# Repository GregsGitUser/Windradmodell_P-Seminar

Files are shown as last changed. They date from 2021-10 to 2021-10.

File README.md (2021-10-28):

# Windradmodell_P-Seminar
CAD-Dateien der von mir erstellten Teile und der Code, der auf dem Arduino Nano läuft. Außerdem noch die source-Dateien für die Platine, die ich für dieses Projekt gemacht habe

Im Rahmen des P-Seminars Physik am ITG 2020-22 mit dem Thema Klimawandel

Wir wollten ein Windradmodell bauen und an diesem verschiedene Messungen durchführen. Als Zusatzfunktion sollte es noch der Windrichtung folgen,
was durch einen Schrittmotor (NEMA 17-03 mit 20Nm und 0,2A) in der Basis des Windrads und einen Zweipunktregler möglich wurde. Zur Ansteuerung wird ein A4988 Treiber verwendet.
Der Microcontroller ist ein Arduino Nano, der als Interface einen Drehenkoder (KY-040) und Kippschalter hat. So kann auch die Regelungsgeschwindigkeit für den Zweipunktregler
eingestellt werden. Informationen können auf einem 16x2 LCD-Bildschirm abgelesen werden, der über I2c (mit I2c Bus) mit dem Microcontroller kommuniziert. 
Ein generisches Gleichstromnetzteil dient als Stromversorgung.

Oben in der Gondel des Windrads ist ein kleiner Generator, dessen Ausgangsleistung an einem Lastwiderstand (>2 Ohm) abfällt.
Die Spannung, welche über dem Widerstand abfällt, kann direkt analog mit dem internen 10-Bit ADC eingelesen werden, weil sie 5V (die Logikspannung des Nanos) nie überschreitet.
Aus diesen Werten kann die insgesamte elektrische Leistung abgeleitet werden. (meistens unter 200mW)

Eine andere Möglichkeit, die Leistung zu bestimmen ist mittels der detektierten Rotorblätter. Am Mast sitz ein HC-SR04 Ultraschallsensor, der zeitgleich in 5-Sekunden Intervallen
die Rotorblätter zählt und das Ergebnis dann auf dem LCD ausgibt. So kann die auf zwei Arten gemessene Leistung verglichen werden.

Alle hier aufgelisteten 3d-Modelle habe ich in Autodesk Fusion 360 oder SOLIDWORKS designed und auf einem Prusa Mk2 gedruckt. Das Design der Platine habe ich in 
Autodesk EAGLE erstellt und diese anschließend mit dem PCB-GCODE ulp-plugin zuhause gefertigt. Der Arduino Nano wurde mit der Arduino IDE programmiert.
Die Aluteile, die Propellernaben für unterschiedlich viele Rotorblätter, und die Basis für den Schrittmotor haben wir in Kooperation mit Autoliv gefertigt.

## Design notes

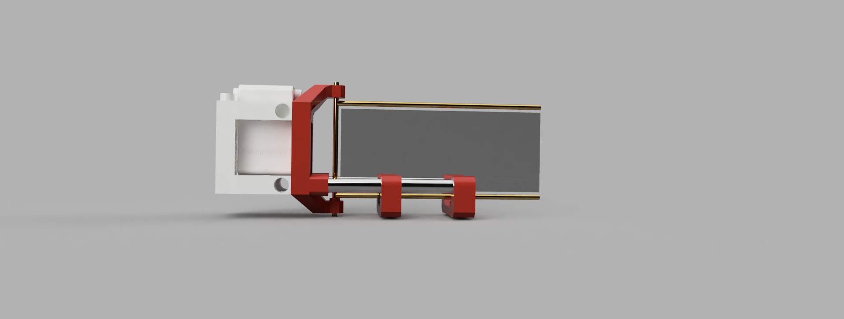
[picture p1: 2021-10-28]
renders/schule_fahnenhalter-2_seite.png

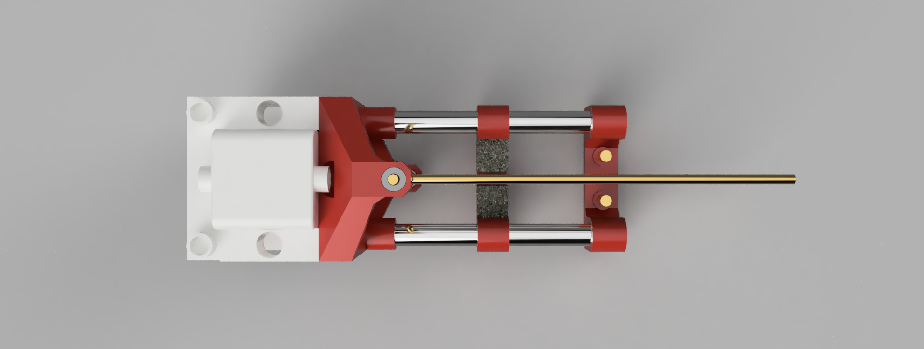
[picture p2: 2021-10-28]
renders/oben.PNG

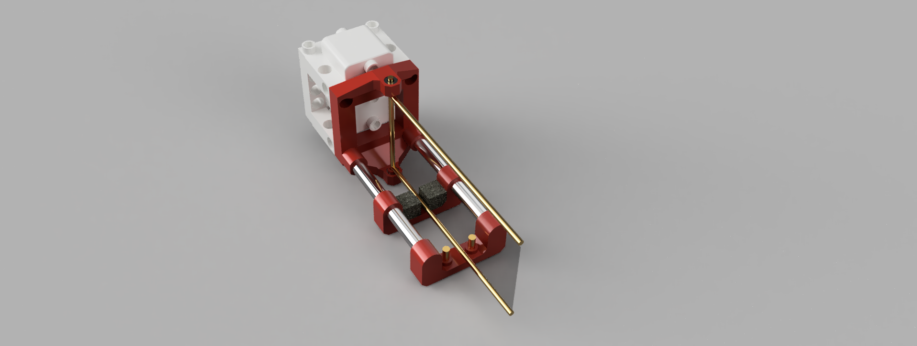
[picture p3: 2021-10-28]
renders/schule_fahnenhalter-2_schräg.png

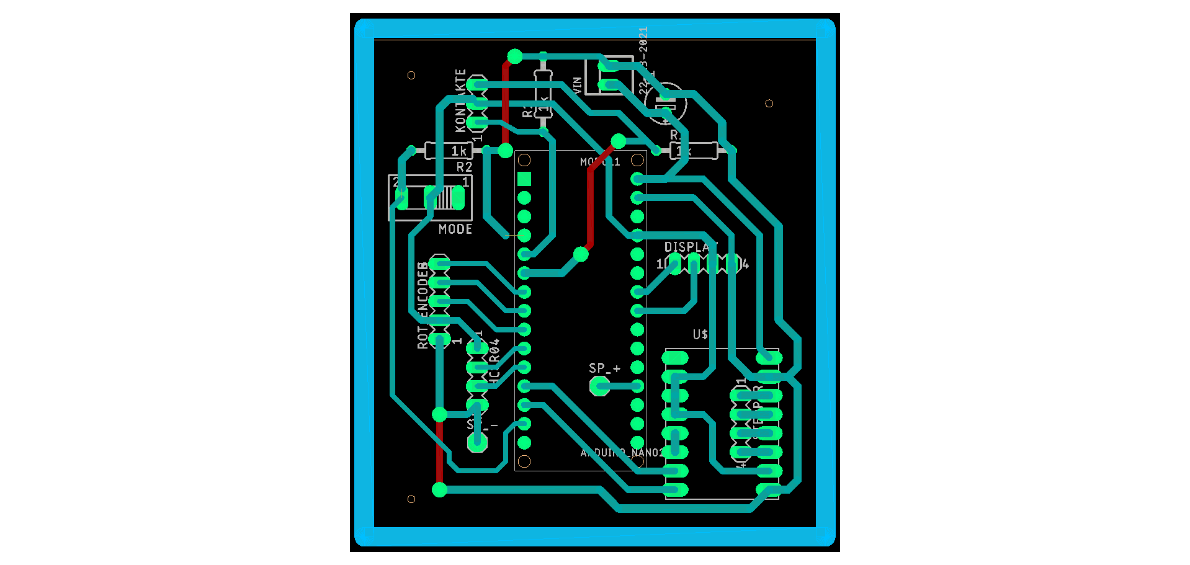
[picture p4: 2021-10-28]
platine/Platine.png

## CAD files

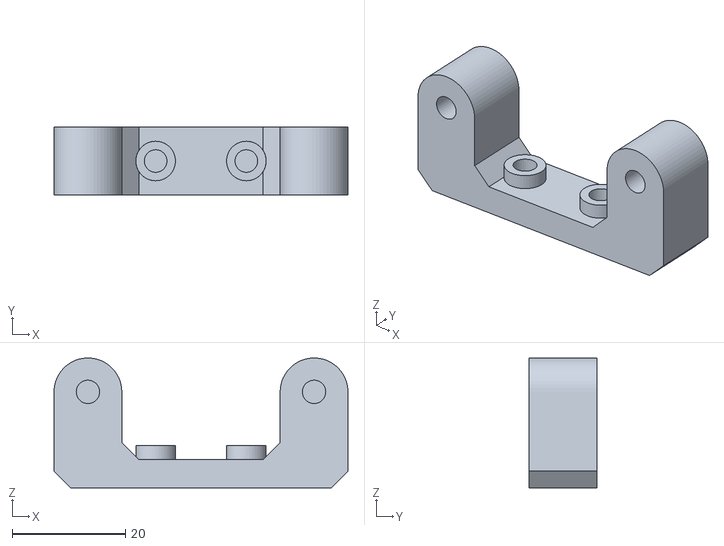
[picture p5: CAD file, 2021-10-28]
3d-modelle/fahnenhalter_gondel/bruecke_außen.stl
52.0 x 12.0 x 23.0

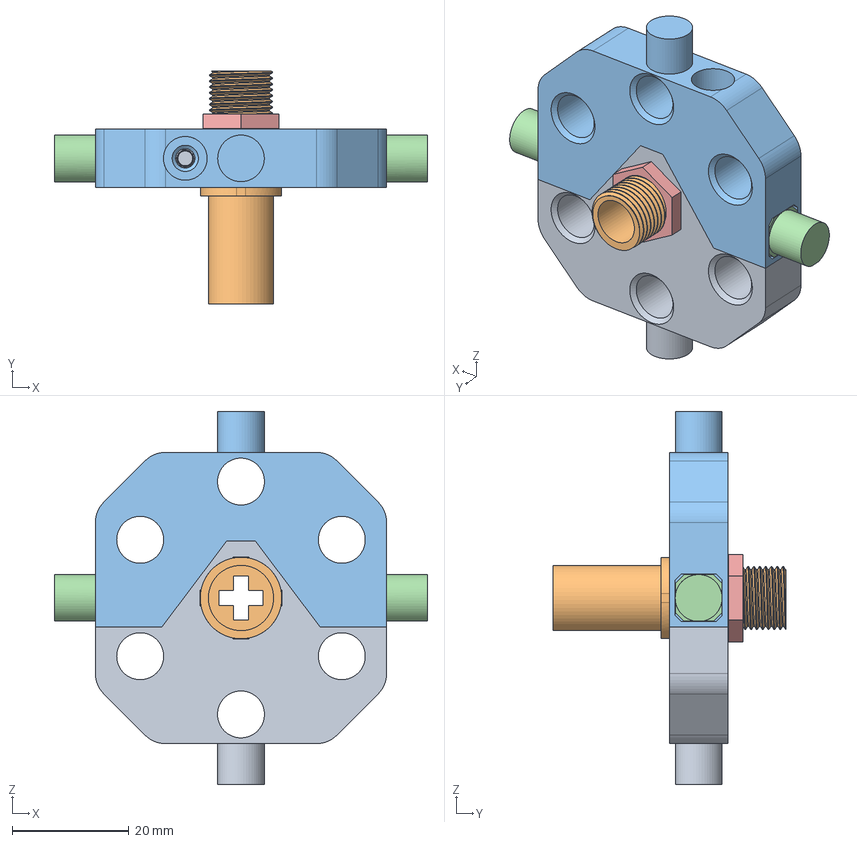
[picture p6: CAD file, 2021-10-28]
3d-modelle/nabe_4_Rotorblaetter.step
64.0 x 40.0 x 64.0 mm

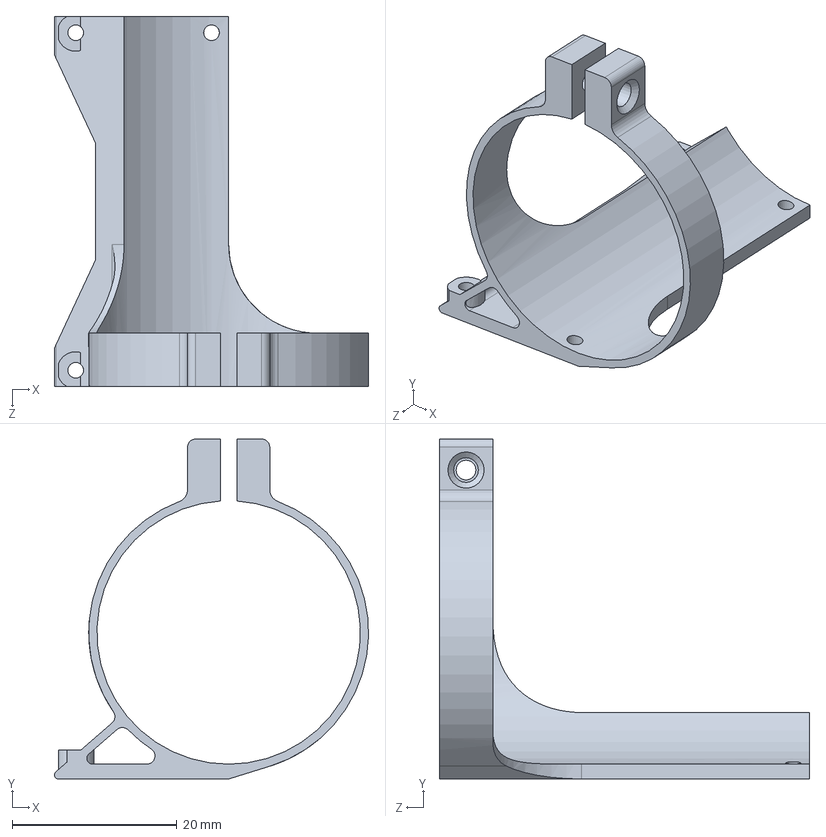
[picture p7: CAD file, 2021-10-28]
3d-modelle/ultraschallhalter/ultraschallhalter.SLDPRT
38.2 x 41.3 x 45.0 mm

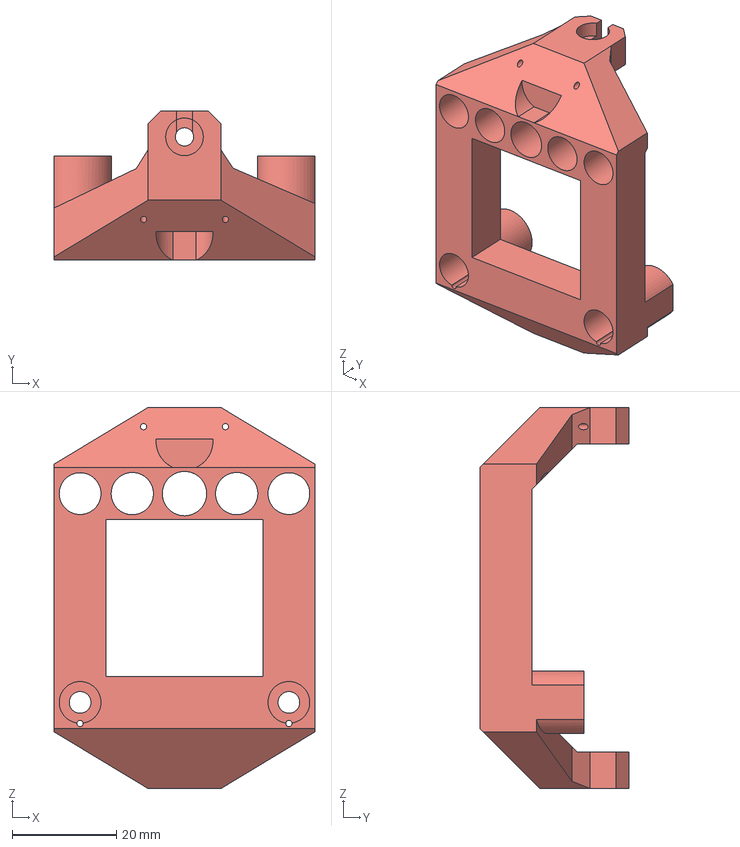
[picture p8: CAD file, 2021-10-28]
3d-modelle/fahnenhalter_gondel/hauptkörper2.step
50.0 x 28.6 x 73.0 mm

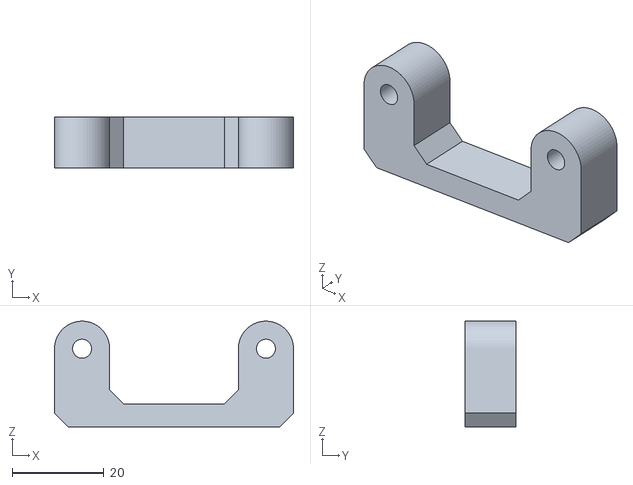
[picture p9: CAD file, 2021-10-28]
3d-modelle/fahnenhalter_gondel/bruecke_mitte.stl
52.0 x 11.0 x 23.0

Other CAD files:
3d-modelle/fahnenhalter_gondel/hauptkörper2.stl
3d-modelle/ultraschallhalter/ultraschallhalter.STL

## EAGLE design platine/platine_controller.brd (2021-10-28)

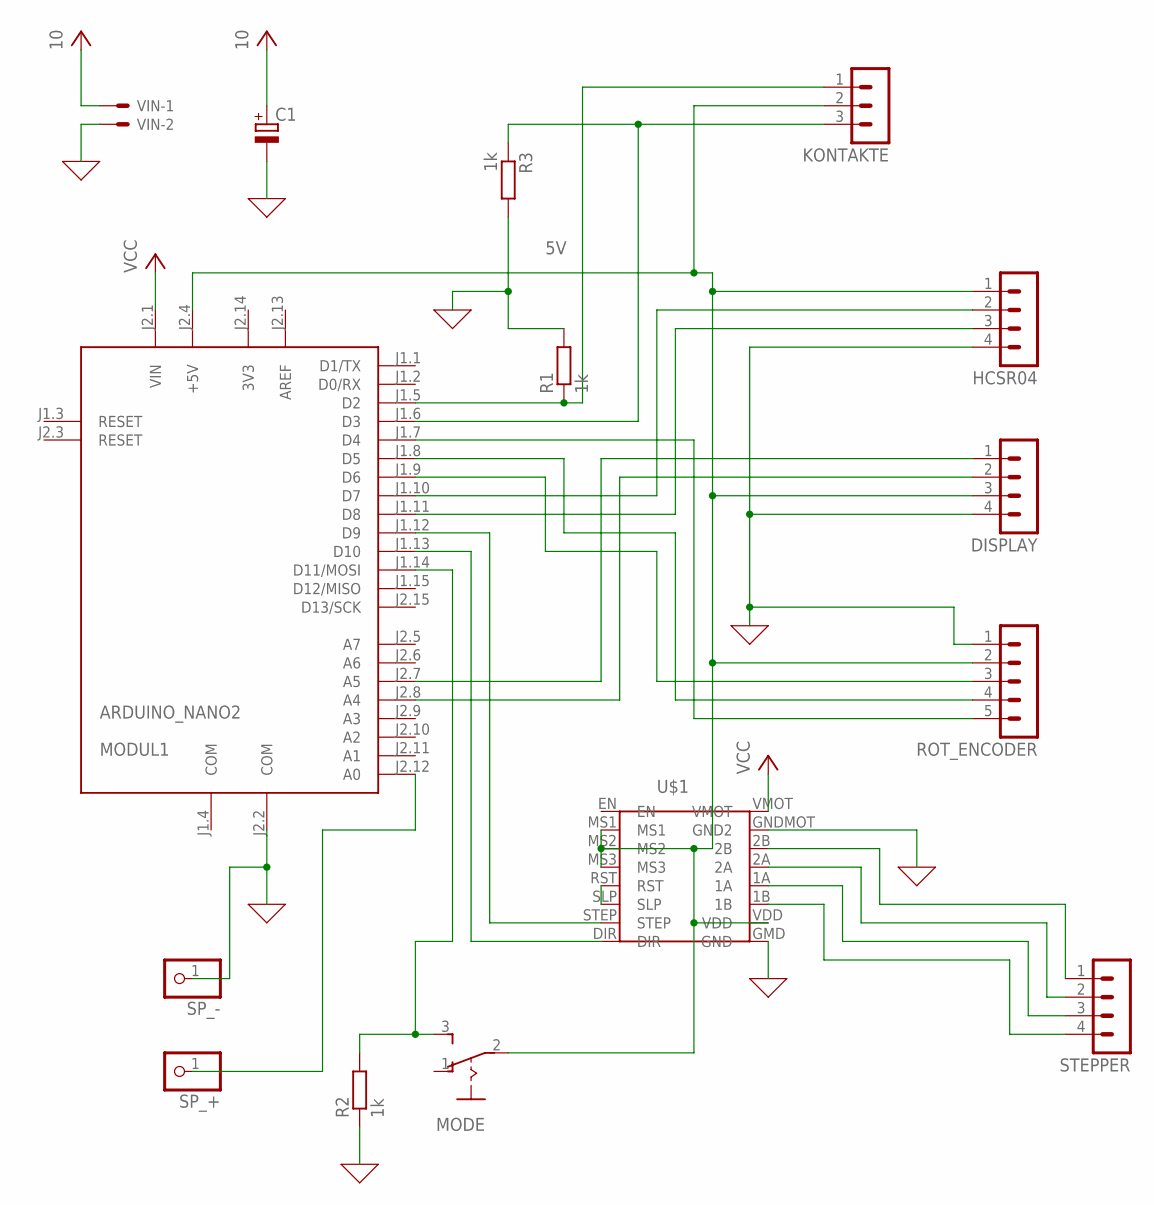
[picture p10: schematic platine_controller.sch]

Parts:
C1: CPOL-EUE2,5-6E; E2,5-6E
DISPLAY: MA04-1
HCSR04: MA04-1
KONTAKTE: MA03-1
MODE: 255SB
MODUL1: ARDUINO_NANO2
R1, R2, R3: 1k; 0207/10
ROT_ENCODER: MA05-1
SP_+: PINHD-1X1; 1X01
SP_-: PINHD-1X1; 1X01
STEPPER: MA04-1
U$1: A4988
VIN: 22-23-2021

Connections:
3V3: MODUL1.J2.14 (3V3)
5V: DISPLAY.3, HCSR04.1, KONTAKTE.2, MODE.2, MODUL1.J2.4 (+5V), ROT_ENCODER.2, U$1.MS1, U$1.MS2, U$1.MS3, U$1.VDD
AREF: MODUL1.J2.13 (AREF)
COM: C1.-, DISPLAY.4, HCSR04.4, MODUL1.J1.4 (COM), MODUL1.J2.2 (COM), R1.2, R2.1, R3.2, ROT_ENCODER.1, SP_-.1, U$1.GMD (GND), U$1.GNDMOT (GND2), VIN.2
unnamed: MODUL1.J1.7 (D4), ROT_ENCODER.5
unnamed: STEPPER.1, U$1.2B
unnamed: MODUL1.J1.12 (D9), U$1.STEP
unnamed: MODUL1.J1.13 (D10), U$1.DIR
unnamed: U$1.RST, U$1.SLP
unnamed: STEPPER.2, U$1.2A
unnamed: STEPPER.3, U$1.1A
unnamed: STEPPER.4, U$1.1B
unnamed: HCSR04.3, MODUL1.J1.11 (D8)
unnamed: HCSR04.2, MODUL1.J1.10 (D7)
unnamed: DISPLAY.1, MODUL1.J2.7 (A5)
unnamed: DISPLAY.2, MODUL1.J2.8 (A4)
unnamed: MODUL1.J1.9 (D6), ROT_ENCODER.3
unnamed: MODUL1.J1.8 (D5), ROT_ENCODER.4
unnamed: KONTAKTE.3, MODUL1.J1.6 (D3), R3.1
unnamed: KONTAKTE.1, MODUL1.J1.5 (D2), R1.1
unnamed: MODE.3 (S), MODUL1.J1.14 (D11/MOSI), R2.2
unnamed: MODUL1.J2.12 (A0), SP_+.1
VCC: C1.+, MODUL1.J2.1 (VIN), U$1.VMOT, VIN.1

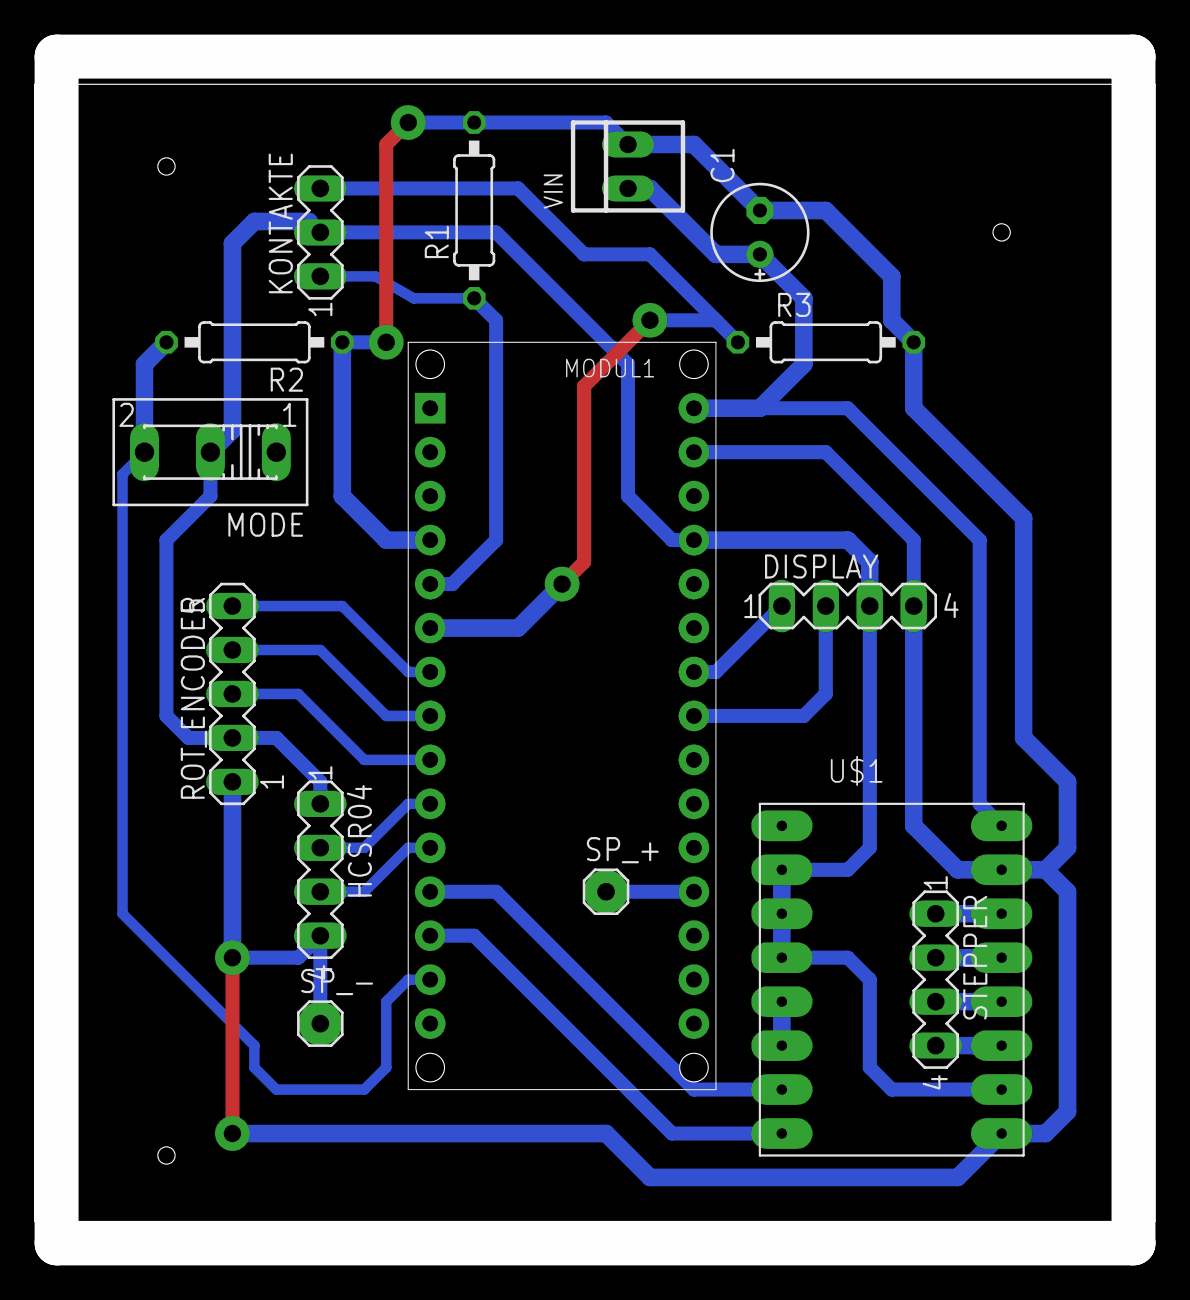
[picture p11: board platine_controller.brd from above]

Board: 2 copper layers, 64.8 x 68.6 mm, 15 parts (0 on the bottom side), 21 nets.

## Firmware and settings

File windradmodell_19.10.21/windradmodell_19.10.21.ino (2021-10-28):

/*  Im Rahmen des P-Seminars 2P_Physik 2020-22 am ITG Dachau
 *  von Gregor Sellschopp
 *  läuft auf dem Windradmodell
 *  Die beiden grundsätzlichen Modi: Nachführen oder Messen (der Umdrehung und Leistung)
 *  Als Eingabemöglichkeiten gibt es den Drehschalter mit Knopffunktion und einen Kippschalter, um zwischen den Hauptmodi zu wechseln
 *  Finale Version vom 18.10.2021
 */

#include <Wire.h> // Wire Bibliothek einbinden
#include <LiquidCrystal_I2C.h> // LiquidCrystal_I2C Bibliothek einbinden
LiquidCrystal_I2C lcd(0x27, 16, 2); //Hier wird festgelegt um was für einen Display es sich handelt.
//In diesem Fall eines mit 16 Zeichen in 2 Zeilen und der HEX-Adresse 0x27.
//Für ein vierzeiliges I2C-LCD verwendet man den Code "LiquidCrystal_I2C lcd(0x27, 20, 4)"
// SDA -> A4
// SCL -> A5

int Index;
const float resolution = 1.8; // Schrittweite des Schrittmotors in Grad. Ein 'step' entspricht also 1.8 Grad.
int z = 0;
int winkel = 0;
int laenge = 1;
double stepperPos = 0.000; // aktuelle Position des Schrittmotors
// Anschlüsse zur Ansteuerung des Zweipunktreglers und Schrittmotors
const int enable = 4;
const int step = 9;
const int direction = 10;
const int kontakt_rechts = 3;
const int kontakt_links = 2;

// Anschlüsse und Variablen des Dreh-encoders
int Pin_clk_Letzter;
int Pin_clk_Aktuell;
const int pin_clk = 4;
const int pin_dt = 5;
const int button_pin = 6;
int counter = 0;

// Anschlüsse und Variablen des Ultraschallsensors
const int trigger = 7;
const int echo = 12;
long dauer = 0;
long entfernung = 0;
int umdrehungen;
int grenzwert = 15;

// Anschlüssen und Variablen zur elektronischen Messung
float widerstand = 1.70; // Wert des Lastwiderstandes in Ohm
float leistung; // Leistung, die bei diesem Widerstand abfällt
float stromstaerke; // theoretische, berechnete Stromstärke
const int sp_pin_pos = A0; // Pin, der die über dem Widerstand abgefallene Spannung ausliest. Beim Anschließen auf Polarität achten!

int messdauer = 5; // Messdauer in Sekunden

int positionen[] = {0, 5, 10, 15, 20, 25, 35, 45}; // Positionen, die im Mess-Modus angefahren werden
int anzahl; // anzahl der Positionen im Array positionen
boolean geeicht = false;

int ANTI_OSZ_DEL = 0; // kurzer delay um Oszillieren vorzubeugen; Zeitdauer in Millisekunden; Genaue Auswahl erfolgt im Menü

// Pins des Schiebeschalters für die Auswahl eines Modus
int modus = 11;

void setup()
{
  Serial.begin(115200); //Baudrate beim Anschließen an einen Computer; diese muss in der Arduino IDE richtig eingestellt werden, um im seriellen Monitor vernünftige Ausgaben zu erhalten.
  // Kontakte am Windrad für den Zweipunktregler. Beide werden als digitale Eingänge gesetzt.
  pinMode(kontakt_rechts, INPUT);
  pinMode(kontakt_links, INPUT);

  // pins zur Steuerung des A4988 (Schrittmotortreibers)
  pinMode(enable, OUTPUT); //Enable; nicht in verwendung; kann den Treiber insgesamt ausschalten
  pinMode(step, OUTPUT); //Step
  pinMode(direction, OUTPUT); //RIchtung

  // pins zur Steuerung des Ultraschallsensors
  pinMode(trigger, OUTPUT);
  pinMode(echo, INPUT);

  // Eingangs-Pins des Drehschalters
  pinMode (pin_clk, INPUT);
  pinMode (pin_dt, INPUT);
  pinMode (button_pin, INPUT);
  pinMode(modus, INPUT);

  // ...und deren Pull-Up Widerstände aktiviert
  digitalWrite(pin_clk, true);
  digitalWrite(pin_dt, true);
  digitalWrite(button_pin, true);
  digitalWrite(modus, true);
  digitalWrite(enable, LOW);

  lcd.init(); //Im Setup wird der LCD gestartet
  lcd.backlight(); //Hintergrundbeleuchtung einschalten
  lcd.clear(); // Jegliche Inhalte auf dem Bildschirm löschen

  Pin_clk_Letzter = digitalRead(pin_clk); // letzter Status des Drehschalters wird auch gespeichert, um ihn später mit dem aktuellen zu vergleichen und so Änderungen festzustellen.

  for (byte i = 0; i < (sizeof(positionen) / sizeof(positionen[0])); i++) {
    anzahl++;
  }

  eichen();
  antiOsz(); // Hier kann eine mögliche Verlangsamung der Schrittmotorbewegungen festgelegt werden, um Oszillation des Zweipunktreglers zu vermeiden
}

void loop() // Diese Schleife wird dauerhaft wiederholt
{
  if (digitalRead(modus)) nachfuehren(); // Hier wird der Kippschalter digital eingelesen, der über den Programmmodus entscheidet
  else messen();
}

void nachfuehren() ////////////////////////////////////////////////////////////////////////////////////// Diese Methode wird im Nachfuehren-Modus aufgerufen
{
  // Hier werden die Messwerte auf dem LCD-Bildschirm ausgegeben
  lcd.setCursor(0, 0);
  lcd.print("Modus:");
  lcd.setCursor(0, 1);
  lcd.print("Nachfuehren");

  while (digitalRead(kontakt_rechts) == HIGH) // Wenn die Fahne die rechte Grenze erreicht
  {
    delay(ANTI_OSZ_DEL); // Soll Oszillation verhindern (kann in der 'antiOsz' Methode festgelegt werden)
    digitalWrite(direction, LOW);
    Serial.println("RECHTS_HIGH");

    digitalWrite(step, HIGH);
    delayMicroseconds(500);
    digitalWrite(step, LOW);
    delayMicroseconds(500);
    stepperPos = stepperPos + 0.1125;
  }
  while (digitalRead(kontakt_links) == HIGH) // Wenn die Fahne die linke Grenze erreicht
  {
    delay(ANTI_OSZ_DEL);  // Soll Oszillation verhindern (kann in der 'antiOsz' Methode festgelegt werden)
    digitalWrite(direction, HIGH);
    Serial.println("LINKS_HIGH");

    digitalWrite(step, HIGH);
    delayMicroseconds(500);
    digitalWrite(step, LOW);
    delayMicroseconds(500);
    stepperPos = stepperPos - 0.1125;
  }
}

void messen() ///////////////////////////////////////////////////////////////////////////////////////////////// Diese Methode wird im Mess-Modus aufgerufen
{
  unsigned long t; // speichert eine Zeitreferenz
  // Ausgaben über die serielle Schnittstelle des Arduinos
  Serial.print("------------------messen---stepperPos: ");
  Serial.print(stepperPos);
  Serial.print(" anzahl: ");
  Serial.println(anzahl);

  lcd.clear();
  lcd.setCursor(0, 0);
  lcd.print("Messzyklus Start");

  t = millis();
  while (millis() < t + 2000) {} // Zeit für den Stepper um aus einer möglichen starken Auslenkung in die Ausgangsposition zu kommen.

  for (int j = 0; j < anzahl; j++) // geht die Positonen in 5 Grad Schritten durch -> siehe Array 'positionen'
  {
    int pos = positionen[j];
    // Hier wird vorangekündigt, welcher Winkel als nächstes gemessen wird. Der Messintervall beträgt 5 Sekunden.
    lcd.clear();
    lcd.setCursor(0, 0);
    lcd.print("Jetzt kommen");
    lcd.setCursor(0, 1);
    lcd.print(pos);
    lcd.setCursor(4, 1);
    lcd.print("Grad");

    if (stepperPos < pos)// fährt in die richtige Position
    {
      while (stepperPos < pos)
      {
        delay(ANTI_OSZ_DEL); // Soll Oszillation verhindern (kann in der 'antiOsz' Methode festgelegt werden)
        digitalWrite(direction, HIGH);
        digitalWrite(step, HIGH);
        delayMicroseconds(500);
        digitalWrite(step, LOW);
        delayMicroseconds(500);
        stepperPos = stepperPos + 0.1125;
      }
    }
    else if (stepperPos > pos)
    {
      while (stepperPos > pos)
      {
        delay(ANTI_OSZ_DEL); // Soll Oszillation verhindern (kann in der 'antiOsz' Methode festgelegt werden)
        digitalWrite(direction, LOW);
        digitalWrite(step, HIGH);
        delayMicroseconds(500);
        digitalWrite(step, LOW);
        delayMicroseconds(500);
        stepperPos = stepperPos - 0.1125;
      }
    }
    t = millis();
    while (millis() < t + 2000) {} // Zeit für den Stepper um aus einer möglichen starken Auslenkung in die Ausgangsposition zu kommen.
    // Ausgaben über die serielle Schnittstelle des Arduinos
    Serial.print("  stepperPos: ");
    Serial.print(stepperPos); // ist jetzt in der richtigen Position
    Serial.print("  pos: " );
    Serial.print(pos);

    umdrehungen = 0; // Anzahl der erkannten Flügelblätter
    float spannung = 0; // über dem Lastwiderstand abfallende Spannung
    unsigned long k = millis();

    int z = 0;
    boolean vorherBlockiert = false; // Status der vorherigen Messung wird gespeichert, damit man nicht denselben Flügel zwei Mal detektiert und als Zwei erkennt.
    while ( k + messdauer * 1000 > millis() ) // In dieser Schleife wird auf zwei Arten die Leistung des Windrads gemessen:
    {
      z++;
      // einmal über Ultraschall
      for (int m = 0; m < 2; m++)
      {
        digitalWrite(trigger, LOW);
        t = millis();
        while (millis() < t + 5) {}
        digitalWrite(trigger, HIGH);

        t = millis();
        while (millis() < t + 10) {}
        digitalWrite(trigger, LOW);

        dauer = pulseIn(echo, HIGH, 3000);
        entfernung = entfernung + (dauer / 2) * 0.03432;
      }
      entfernung = entfernung / 2;
      Serial.println(entfernung);

      if (entfernung < grenzwert && entfernung > 0 && !vorherBlockiert) // Bewirkt, dass ein Flügel nur beim ersten Durchgang erkannt wird. Es muss wieder frei werden, damit ein neuer Fügel erkannt wird.
      {
        umdrehungen++;
        vorherBlockiert = true;
      }
      if (entfernung > grenzwert || entfernung == 0) vorherBlockiert = false;

      // und über die elektrische Leistung
      spannung = spannung + analogRead(sp_pin_pos) * 5.0 / 1023; // analoges Einlesen der Spannung, die über dem Lastwiderstand abfällt
    }
    // Umrechnungen, um die Stromstärke zu erschließen
    spannung = spannung / z;
    stromstaerke = spannung / widerstand;
    leistung = stromstaerke * spannung;
    // Hier werden die Messwerte einer Position auf dem LCD-Bildschirm ausgegeben
    lcd.clear();
    lcd.setCursor(0, 0);// In diesem Fall bedeutet (0,0) das erste Zeichen in der ersten Zeile.
    lcd.print("Flueg./5s: ");
    lcd.setCursor(11, 0);
    lcd.print(umdrehungen);
    lcd.setCursor(0, 1);
    lcd.print("P in mW: ");
    lcd.setCursor(10, 1);
    lcd.print(leistung * 1000);

    t = millis();
    while (millis() < t + 5000) {}
    // Ausgaben über die serielle Schnittstelle des Arduinos
    Serial.print("  Umdrehungen in 5 sek.: ");
    Serial.print(umdrehungen);
    Serial.print("    |    Leistung: ");
    Serial.print(leistung);
    Serial.print(",  Spannung: ");
    Serial.print(spannung);
    Serial.print(",  theoretische Stromstärke: ");
    Serial.println(stromstaerke);

    Serial.println();
  }
  lcd.clear();
}

void eichen() ///////////////////////////////////////////////////////////////////////////////////////////////////// Diese Methode legt die Ausgangspositionen für die weiteren Prozesse fest.
{
  lcd.setCursor(0, 0);
  lcd.print("nullen...");
  while (!geeicht)
  {
    winkel = counter / 2;
    Serial.print("eichen    ");
    Serial.print(winkel);
    Serial.print("    ");
    Serial.println(stepperPos);
    Pin_clk_Aktuell = digitalRead(pin_clk);

    // Überprüfung des Dreh-encoders auf Änderung
    if (Pin_clk_Aktuell != Pin_clk_Letzter)
    {
      if (digitalRead(pin_dt) != Pin_clk_Aktuell)
      {
        // Pin_CLK hat sich zuerst verändert      => die eine Drehrichtung
        counter ++;
        digitalWrite(direction, LOW);
        while (counter / 2 > stepperPos + 0.1125 / 2)
        {
          digitalWrite(step, HIGH);
          delayMicroseconds(500);
          digitalWrite(step, LOW);
          delayMicroseconds(500);
          stepperPos = stepperPos + 0.1125;
        }
      }
      else
      { // Andernfalls hat sich Pin_DT zuerst verändert       => die andere Drehrichtung
        counter--;
        digitalWrite(10, HIGH);
        while (counter / 2 < stepperPos - 0.1125 / 2)
        {
          digitalWrite(step, HIGH);
          delayMicroseconds(500);
          digitalWrite(step, LOW);
          delayMicroseconds(500);
          stepperPos = stepperPos - 0.1125;
        }
      }
    }
    if (!digitalRead(button_pin))// && winkel != 0) // Durch Drücken des encoders wird die Position des Steppers genullt.
    {
      winkel = 0;
      stepperPos = 0;
      geeicht = true;
      Serial.println("erfolgreich genullt");
      delay(500);
    }
    Pin_clk_Letzter = Pin_clk_Aktuell;
  }
  lcd.clear();
}
int antiOsz() { /////////////////////////////////////////////////////////////////////////////////////////////////////////////// Hier kann eine mögliche Verlangsamung festgelegt werden, um Oszillation des Zweipunktreglers zu vermeiden
  lcd.clear();
  lcd.setCursor(0, 0);
  lcd.print("delay gegen");
  lcd.setCursor(0, 1);
  lcd.print("Oszillation?");
  int t = millis();
  boolean antiOszDel = false;
  while (t + 5000 > millis()) {     // falls man eine Verlangsamung einstellen möchte, muss hier der Encoder gedrückt werden. Achtung: das System reagiert nicht sofort, sondern wartet noch den Rest der insgesamt 5 Sekunden ab. Mehrmaliges Drücken zur Sicherheit schadet nicht.
    if (!digitalRead(button_pin)) {
      antiOszDel = true;
    }
  }
  if (antiOszDel) {
    lcd.clear();
    String ANTI_OSZ_DEL_STR;
    lcd.setCursor(0, 0);
    lcd.print("delay: ");
    
    while (digitalRead(button_pin)) { // Solange man den Encoder nicht noch ein Mal drückt, kann der Wert durch Drehen verändert werden.
      if (ANTI_OSZ_DEL < 100)  ANTI_OSZ_DEL_STR = "0" + String(ANTI_OSZ_DEL);   //padding => resultierende Zahl hat immer 3 Stellen => kein clear() nötig => bessere Qualität der Ausgabe
      else  if (ANTI_OSZ_DEL < 10)  ANTI_OSZ_DEL_STR = "00" + ANTI_OSZ_DEL;
      lcd.setCursor(6, 0);
      lcd.print(ANTI_OSZ_DEL_STR);
      Pin_clk_Aktuell = digitalRead(pin_clk);

      // Überprüfung des Dreh-encoders auf Änderung
      if (Pin_clk_Aktuell != Pin_clk_Letzter)
      {
        if (digitalRead(pin_dt) != Pin_clk_Aktuell) ANTI_OSZ_DEL ++; // Wert wird entsprechend des Drehschalters verändert.
        else ANTI_OSZ_DEL --;
        if ( ANTI_OSZ_DEL < 0) ANTI_OSZ_DEL = 0;
      }
      Pin_clk_Letzter = Pin_clk_Aktuell;
      Serial.print("anti-oszillations-delay: ");
      Serial.println(ANTI_OSZ_DEL); // Finale Ausgabe des bestätigten Wertes.
    }
  }
  lcd.clear(); // Alles auf dem Bildschirm wird gelöscht
}

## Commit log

2021-10-28 platinenlayout .brd und .sch plus PNG
    wurden in Autodesk EAGLE erstellt
    [platine_controller.brd, platine_controller.sch]
2021-10-28 auf dem arduino nano laufender programmcode
    grundlegend C++
    kann mit der Arduino IDE geöffnet werden
2021-10-28 Plan für die Gondel
